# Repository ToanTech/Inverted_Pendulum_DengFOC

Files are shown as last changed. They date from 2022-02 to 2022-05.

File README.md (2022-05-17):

# DengFOC动量轮倒立摆项目
**DengFOC动量轮倒立摆**是基于SimpleFOC官方开源的[动量轮倒立摆项目](https://github.com/simplefoc/Arduino-FOC-reaction-wheel-inverted-pendulum)，低成本化和小型化后应用在我开源的[DengFOC](https://github.com/ToanTech/Deng-s-foc-controller)双路无刷电机驱动器上的DengFOC配套项目。

**项目完全开源，你可以根据本Github内容自行白嫖，或者，支持一下灯哥的辛勤劳作，进入灯哥开源TB店购买DengFOC动量轮倒立摆套件，一键配齐。**

[DengFOC动量轮倒立摆套件--链接猛击（进店后在 所有宝贝 处可找到）](https://shop564514875.taobao.com/)



## 1 视频教程

配套本开源项目，灯哥精心制作了全**组装过程视频教程**和**算法原理课**，请点击查看：

[1 DengFOC动量轮倒立摆--效果展示和机械组装](https://www.bilibili.com/video/BV1SU4y1Z72W/)

[2 DengFOC LQR无刷动量轮倒立摆算法原理和DIY实现](https://www.bilibili.com/video/BV1JL4y177Z5/)

## 2 接线

只要你手头有一块DengFOC V3（你可以在TB搜索**灯哥开源**进入店铺购买，或根据[DengFOC开源仓库](https://github.com/ToanTech/Deng-s-foc-controller)的开源资料自制）就可以快速搭接出此项目，项目供电默认电压为16.8V，除DengFOC外，其它电子元器件主要由一个2204无刷电机，两个as5600编码器组成。其接线表格如下：

| 零件 | 接线位置 |
| --- | --- |
| 2204电机 | DengFOC M0位置 |
| 电机端AS5600 | SDA0,SCL0,3V3,GND |
| 摆杆端AS5600 | SDA1,SCL1,3V3,GND |

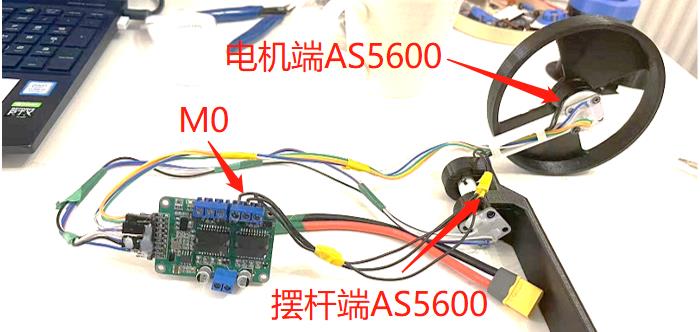
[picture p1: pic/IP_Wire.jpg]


## 3 零件制造

倒立摆的主要零件为3D打印，下载文件夹中的图纸，全100%密度打印即可。

其它零件全部可以在开源文件夹中的"bom表"找到。

## 4 下载程序

下载项目文件夹中的DengFOC_Inverted_Pendulum.ino程序，用Arduino IDE打开，用串口连接DengFOC，即可按照与一般Arduino一致的方法上传。

## 5 调试

### 5.1 初值指定

完成下载程序后，需要对动量轮倒立摆的初始角度进行标定。标定前，首先确保倒立摆处于下垂状态，如图所示：

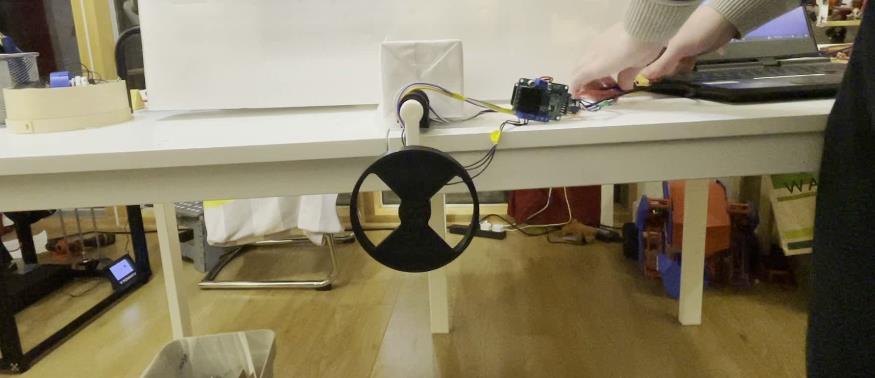
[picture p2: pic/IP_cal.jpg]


接着，注释掉程序中的语句，以确保上电电机不会运动：

`motor.move(target_voltage);`

完成注释后，对DengFOC控制器上电，并按下板子上的“复位”按钮，在电机校准后，Arduino IDE的串口调试器会输出一连串的数值，这就是我们需要的倒立摆初始角度，记录下这个角度，替换掉如图所示的数字3.83：



完成替换后，取消motor.move(target_voltage);这一句代码的注释，使得电机能够运动，重新上传程序，并上电复位，此时倒立摆应该就能正常运转。

### 5.2 LQR参数整定

一般情况下，**LQR控制器的三个参数(即 adjust_ang、 adjust_p_vel 、 adjust_motor_vel)是不需要调节的**，只需要采用和我一样的电机，按照我的打印密度打印零部件，就不需要调整这三个参数。然而，如果你更换电机，亦或者动量轮的打印密度和我的不一样，那么你需要重新调节这三个参数，才能实现稳定。

由于我在程序里做了串口快速调节的部分，因此调节的方法非常简单，下面是调节方法：

**(1)如果你需要调节倒立摆角度稳定的LQR参数：**

在Arduino IDE的串口监视器中输入："A+参数 "即可，如把参数调节到"40"则输入A40

**(2)如果你需要调节倒立摆角速度的LQR参数：**

在Arduino IDE的串口监视器中输入："P+参数 "即可，如把参数调节到"5"则输入P5

**(3)如果你需要调节倒立摆电机速度的LQR参数：**

在Arduino IDE的串口监视器中输入："M+参数 "即可，如把参数调节到"0.01"则输入M0.01

## 6 其它注意事项

如果更换为其他电机，需要重新设置电机极对数

如果自稳效果与倾倒方向相反，证明电机三相线接反，导致电机转向接反，调换三相线中其中两根即可

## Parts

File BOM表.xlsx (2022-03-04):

电控 |  |  | 机械
零件名称 | 数量 | 备注 | 零件名称 | 数量
DengFOC | 1 |  | 摆杆打印件 | 1
AS5600 | 2 |  | 动量轮打印件 | 1
配套传感器径向磁铁 | 2 |  | 基座打印件 | 1
2204云台电机 | 1 | 电机TB地址：https://item.taobao.com/item.htm?id=647180650088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 | 6701ZZ轴承 | 2
杜邦线 | 若干 |  | M3x5螺丝 | 4
4S电池 | 1 |  | M2*5螺丝 | 8
 |  |  | M2x10螺丝 | 1

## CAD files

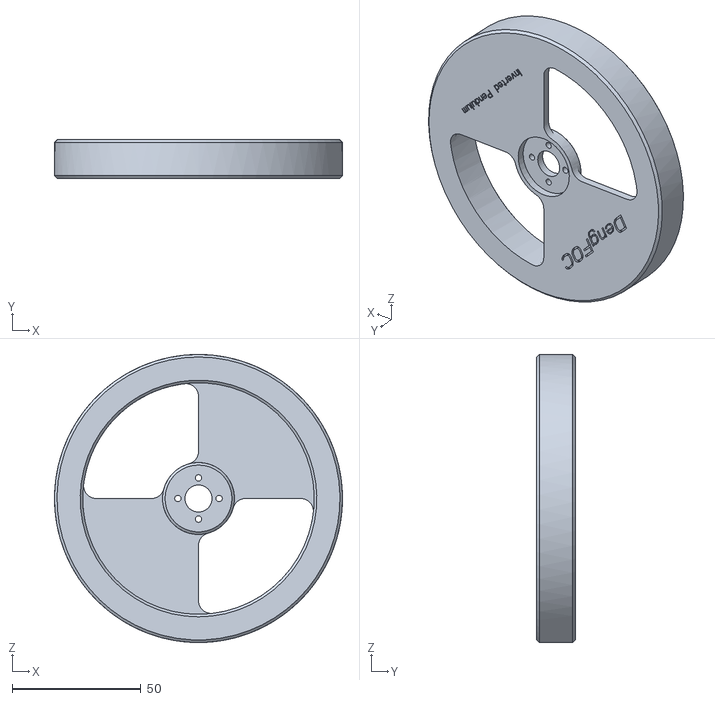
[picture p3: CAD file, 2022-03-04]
3D模型/wheel_main_fit_2204(x1).STL
112.0 x 15.0 x 112.0

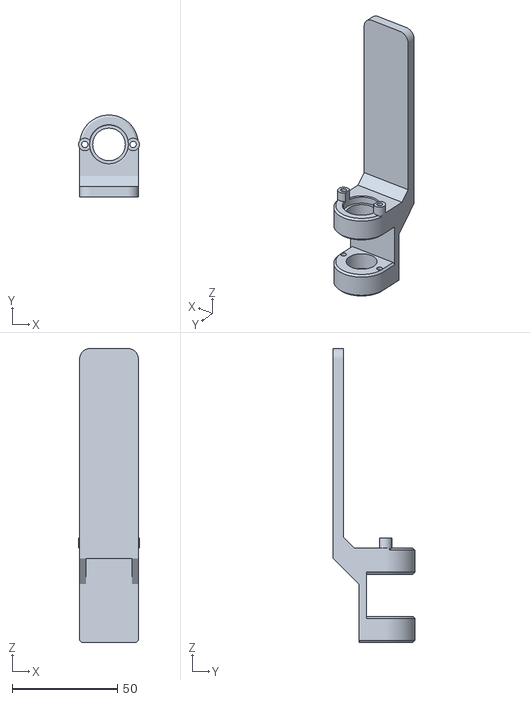
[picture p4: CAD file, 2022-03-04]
3D模型/base_25(x1).stl
29.0 x 39.0 x 140.0

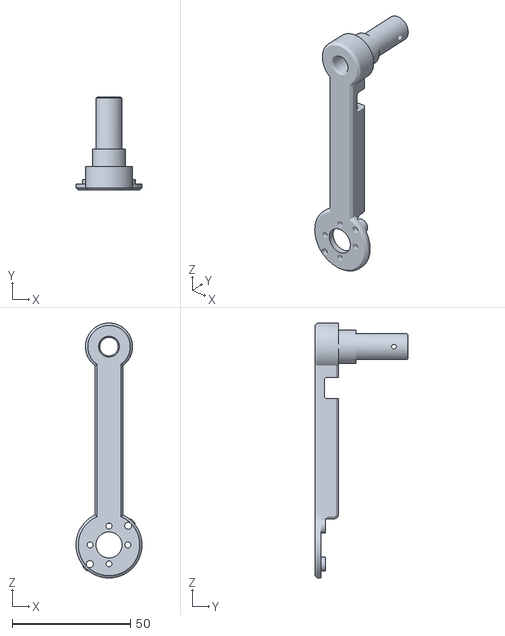
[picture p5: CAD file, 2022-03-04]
3D模型/small_wheel_bar_fit_2204(x1).stl
28.0 x 39.5 x 108.0

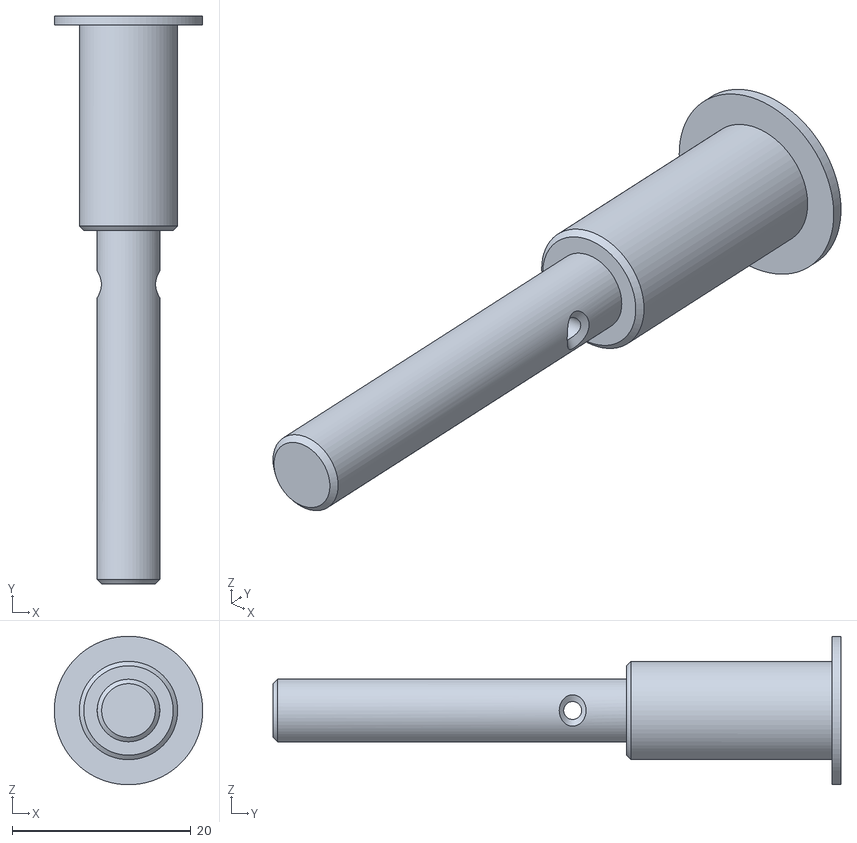
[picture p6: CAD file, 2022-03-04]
3D模型/final_gap_2_20(x1).stl
16.6 x 63.5 x 16.6

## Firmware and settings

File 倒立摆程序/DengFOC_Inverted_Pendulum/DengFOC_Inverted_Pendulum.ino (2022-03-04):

#include <SimpleFOC.h>

// 无刷直流电机初始化
BLDCMotor motor = BLDCMotor(7); //2204电机
// 定义无刷直流驱动器
BLDCDriver3PWM driver = BLDCDriver3PWM(32,33,25,22);
// 电机编码器初始化
MagneticSensorI2C sensor0 = MagneticSensorI2C(AS5600_I2C);
MagneticSensorI2C pendulum = MagneticSensorI2C(AS5600_I2C);
TwoWire I2Cone = TwoWire(0);
TwoWire I2Ctwo = TwoWire(1);

float adjust_ang= 60;
float adjust_p_vel= 3;
float adjust_motor_vel= 0.18;
float adjust_total_ang= 0;   //微调角度
// 通讯命令预设
Commander command = Commander(Serial);
void doTarget_motor_vel(char* cmd) { Serial.print("Change LQR motor_v");command.scalar(&adjust_motor_vel, cmd); }
void doTarget_p_vel(char* cmd) { Serial.print("Change LQR P_v");command.scalar(&adjust_p_vel, cmd); }
void doTarget_ang_vel(char* cmd) { Serial.print("Change LQR ang");command.scalar(&adjust_ang, cmd); }
void doTarget_total_ang(char* cmd) { Serial.print("Change total ang");command.scalar(&adjust_total_ang, cmd); }

void setup() {

  // 初始化电机编码器硬件
  I2Cone.begin(19,18, 400000); 
  I2Ctwo.begin(23,5, 400000);
  sensor0.init(&I2Cone);
  pendulum.init(&I2Ctwo);
  
  // 设置要使用的控制回路类型
  motor.controller = MotionControlType::torque;

  // 将电机连接到编码器
  motor.linkSensor(&sensor0);
  
  // driver
  driver.voltage_power_supply =16.8;
  driver.voltage_limit = 16.8; 
  driver.init();
  // 把电机连接到驱动器上
  motor.linkDriver(&driver);
  Serial.begin(115200);
  motor.useMonitoring(Serial);
  // 初始化运动
  motor.init();
  // 校准编码器并启动FOC
  motor.initFOC();
  command.add('M', doTarget_motor_vel, "adjust_motor_vel");
  command.add('P', doTarget_p_vel, "adjust_p_vel");
  command.add('A', doTarget_ang_vel, "adjust_ang");
  command.add('T',doTarget_total_ang, "adjust_total_ang");
  
}

// 循环下采样计数器
long loop_count = 0;
float target_voltage;

void loop() {
  // ~1ms 
  motor.loopFOC();
  command.run();
   // 控制回路每次~25ms
  if(loop_count++ > 25){
    // 倒立摆传感器读取
    pendulum.update();
    sensor0.update();
    // 计算摆角
    float pendulum_angle = constrainAngle(pendulum.getAngle()-3.83-adjust_total_ang + M_PI);
    Serial.println(pendulum.getAngle());
    //Serial.println(sensor0.getAngle());
    if( abs(pendulum_angle) < 0.5){ // 如果角度足够小稳定
      target_voltage = controllerLQR(pendulum_angle, pendulum.getVelocity(), motor.shaftVelocity());}
    else{ // 倒立摆
      //Serial.println("swing-up");
       // 设置100%的最大电压到电机，以便摆动
      //target_voltage = -_sign(pendulum.getVelocity())*motor.voltage_limit*1;
      target_voltage = -_sign(pendulum.getVelocity())*16.8;
      //Serial.println(target_voltage);
      //target_voltage=0;
    }
     // 将目标电压设置到电机上
    motor.move(target_voltage);
    // 重置计数器
    loop_count=0;
  }
   

}

// 函数限制-和之间的夹角，以-180度和180度表示
float constrainAngle(float x){
    x = fmod(x + M_PI, _2PI);
    if (x < 0)
        x += _2PI;
    return x - M_PI;
}

// LQR稳定控制器功能
// 计算需要设置电机的电压，以稳定摆
float controllerLQR(float p_angle, float p_vel, float m_vel){
  // 如果角度可控
  // 计算控制律 
  // LQR controller u = k*x
  //  - k = [40, 7, 0.3]
  //  - x = [摆角，摆速度，电机速度]' 
  float u =  adjust_ang*p_angle + adjust_p_vel*p_vel + adjust_motor_vel*m_vel;
  // 限制设定给电机的电压
  //if(abs(u) > motor.voltage_limit*1) u = _sign(u)*motor.voltage_limit*1;
  if(abs(u) > driver.voltage_power_supply*0.7) u = _sign(u)*driver.voltage_power_supply*0.7;
  return u;
}
